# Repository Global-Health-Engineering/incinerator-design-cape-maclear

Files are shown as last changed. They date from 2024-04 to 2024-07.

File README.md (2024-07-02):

# incinerator-design-cape-maclear
<!-- badges: start -->


<!-- badges: end -->

<h1> Development of a Low-Cost Incinerator in Cape Maclear, Malawi </h1>

<b>Contributors</b>  
- Mosè Peduzzi <a href="https://orcid.org/0009-0004-6055-3835">
ORCID logo 0009-0004-6055-3835
</a> *author*  
- Jakub Tkaczuk <a href="https://orcid.org/0000-0001-7997-9423">
ORCID logo 0000-0001-7997-9423
</a> *supervisor, maintainer, developer*  
- Elizabeth Tilley <a href="https://orcid.org/0000-0002-2095-9724">
ORCID logo 0000-0002-2095-9724
</a> *supervisor*  

<p align="middle"> 

<br><br>
<b>Complete description of system design, functionalities, operation, and maintenance is available on:<br \>
<a href="https://global-health-engineering.github.io/incinerator-design-cape-maclear/">Github pages</a>.
</b>
<br><br>
It compliments the openly-accessible master’s thesis, available on the<br \>  
<a href="https://www.research-collection.ethz.ch/handle/20.500.11850/670633">ETH Research Collection</a>
<br><br>
and the introduction video available on<br \>
<a href="https://www.youtube.com/watch?v=6FmEJcynxZE">Youtube</a>.
</p>

# Background

This repository presents the construction of a modified De Montfort Incinerator Mark 8A, designed and built between October and December 2023 in Cape Maclear, Malawi. The incinerator has several modifications implemented, compared to the original design, e.g., the ash collection drawer and the cyclone separator to filter the flue gases.

The construction of the incinerator is part of a broader project conducted by Global Health Engineering, an ETH research group, aiming to introduce regular waste collection in the township of Cape Maclear, Malawi, ensuring safe waste disposal and minimizing environmental contamination. The incinerator constructed within this work reduces waste volume and makes hazardous waste harmless, emphasizing cost-effectiveness.

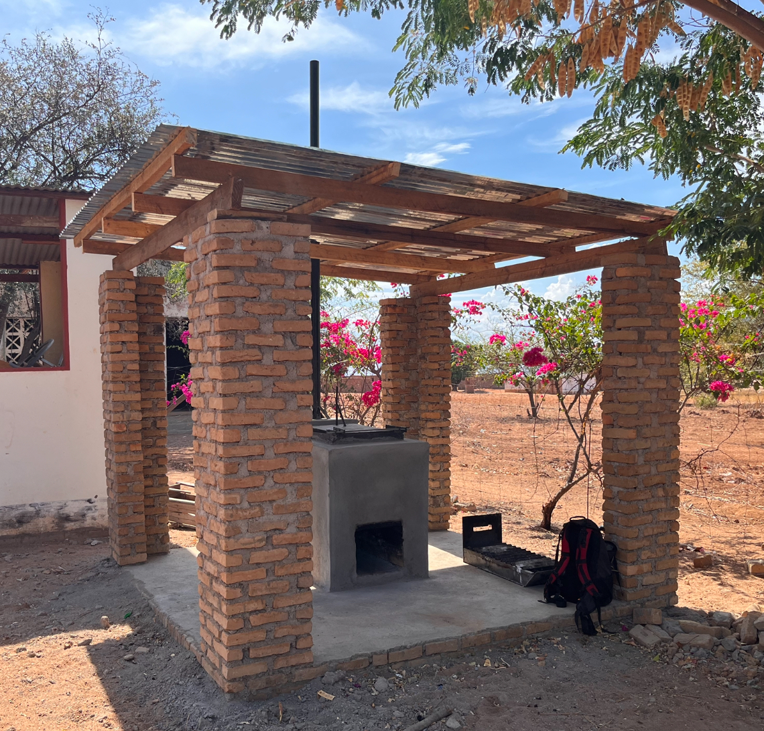
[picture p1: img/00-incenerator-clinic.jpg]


# License

This work is licensed under
[Creative Commons Attribution 4.0 International](https://github.com/Global-Health-Engineering/incinerator-design-cape-maclear/blob/main/LICENSE.md).

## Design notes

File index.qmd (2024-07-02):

---
title: "Low-Cost Incinerator for Cape Maclear, Malawi"
subtitle: "Design, Maintenance, and Operation"
number-sections: true
format: html
---

<!-- badges: start -->


<!-- badges: end -->

<b>Contributors:</b>  
- Mosè Peduzzi <a href="https://orcid.org/0009-0004-6055-3835">
ORCID logo 0009-0004-6055-3835
</a> *author*  
- Jakub Tkaczuk <a href="https://orcid.org/0000-0001-7997-9423">
ORCID logo 0000-0001-7997-9423
</a> *supervisor, maintainer, developer*  
- Elizabeth Tilley <a href="https://orcid.org/0000-0002-2095-9724">
ORCID logo 0000-0002-2095-9724
</a> *supervisor*  

<p align="middle">

<br>
Github repository for this page sits [here](https://github.com/Global-Health-Engineering/incinerator-design-cape-maclear).
</p>

# Introduction {#sec-intro}

This video presents the construction of a modified De Montfort Incinerator Mark 8A, designed and built between October and December 2023 in Cape Maclear, Malawi. The incinerator presents several modifications compared to the original design [^1], e.g., the ash collection drawer [^2] and the cyclone separator to filter the flue gases.

The construction of the incinerator is part of a broader project conducted by Global Health Engineering, an ETH research group, which aims to introduce regular waste collection in the township of Cape Maclear, Malawi, ensuring safe waste disposal and minimizing environmental contamination. This incinerator reduces waste volume and  makes hazardous waste harmless, emphasizing cost-effectiveness.

[^1]: [https://mw-incinerator.info/](https://mw-incinerator.info/)
[^2]: J. Van Den Noortgate, D. Taylor, and G. Yannick, *Incinerator in Health Structures of Low-Income Countries*. Médecins Sans Frontières, 2012. [Link](https://events.development.asia/system/files/materials/2020/04/202004-incineration-health-structures-low-income-countries.pdf).

# Incinerator Overview {#sec-overview}

The incinerator built within this work is a small-size incinerator, composed of a structure of refractory bricks and cement with a metal frame on the top. The interior space is divided into two combustion chambers; the first can be accessed by the operator through a door located at its top, allowing for inserting of a new waste bag. The second combustion chamber and the attached cyclone separator remain inaccessible to the operator and are intended solely for to treat the fumes. The purpose of the second combustion chamber is to reduce carbon monoxide to carbon dioxide through secondary combustion (and combustion time increase), while the cyclone separator allow to reduce the particulate matter (PM) in the fume gasses.

The incinerators can burn about 3.5 kg/h of waste, reaching temperature of 770°C. The mass of the ashes produced by the incinerators represent about 20-30% of total mass of waste burnt.

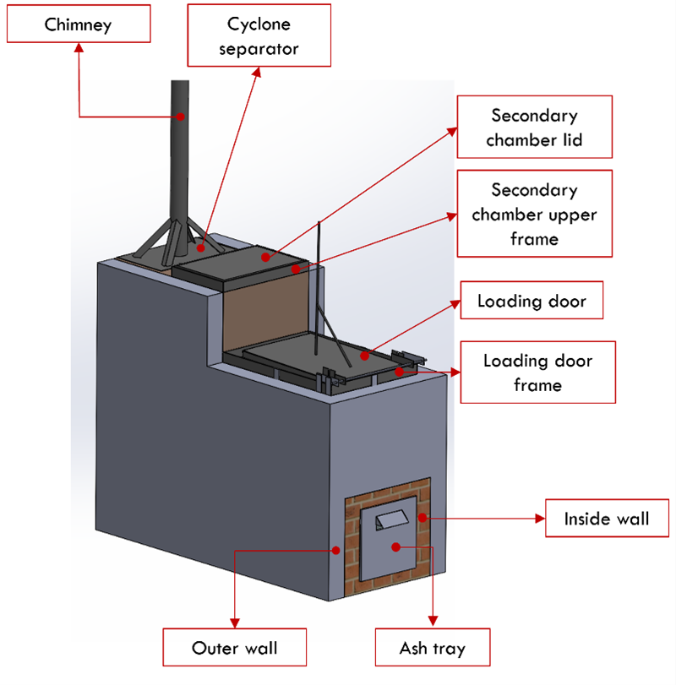
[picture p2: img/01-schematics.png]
Figure 1: Modified De Montfort incinerator Mark 8A with integrated cyclone separator in the back and removable ash tray on the bottom of the combustion chamber.


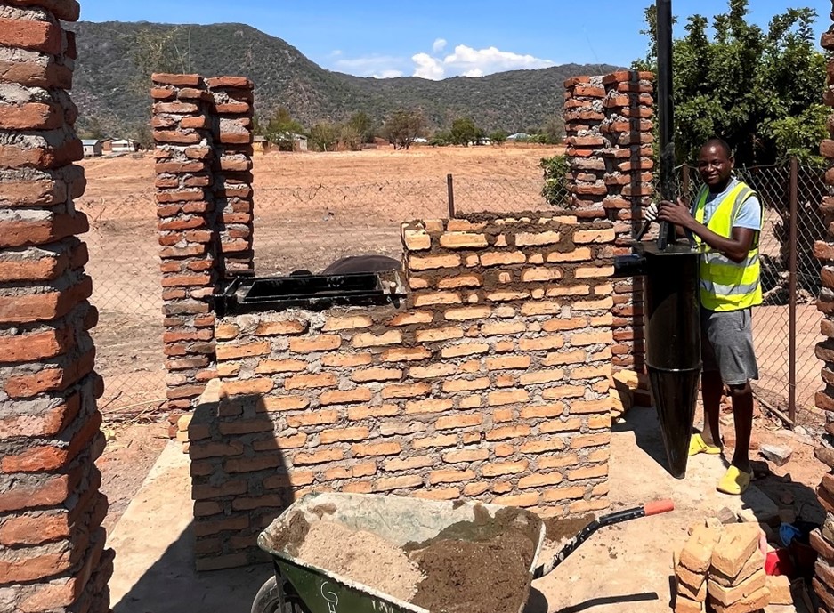
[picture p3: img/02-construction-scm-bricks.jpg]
Figure 2: Incinerator during construction.


# Part List {#sec-part-list}

| No. | Item | Specs | Qty. | Source | Cost per unit (USD) | Total Cost (USD) |
|-----|---|---|---|---|---|---|
| 1 | Metal U-Channel | L x W x H: 100 mm x 60 mm x 6 m | 1 | DeeKay | 85.29 | 85.29 |
| 2 | Angle Iron 30x30x3 mm 6 m | L x W x T: 30 mm x 30 mm x 3 mm x 6 m | 1 | DeeKay | 14.71 | 14.71 |
| 3 | Metal plate | L x W x H: 2400 mm x 1200 mm x 3 mm | 1 | DeeKay | 126.47 | 126.47 |
| 4 | Metal tube with a diameter| D x L: 75 mm x 3 m | 1 | DeeKay | 46.76 | 46.76 |
| 5 | Flat bar | L x W x H: 35 mm x 3 mm x 6 m | 1 | DeeKay | 17.35 | 17.35 |
| 6 | Heat resistent paint | 1 L | 1 | Valmore Paints | 7.47 | 7.47 |
| 7 | Threaded Rod | D x L: M 10 x 1 m | 1 | Build Africa | 6.62 | 6.62 |
| 8 | Bolt | M 10 | 10 | Lilongwe | 0.12 | 1.18 |
| 9 | Washer | M 10 | 2 | Lilongwe | 0.12 | 0.24 |
| 10  | Empty oil barrel | 200 L | 1 | Ndirande market  | 17.65 | 17.65 |
| 11  | Cement bag | 50 kg | 8 | Monkey bay | 11.76 | 94.12 |
| 12  | Sand | 1 ton | 2 | Cape Maclear | 2.94 | 5.88 |
| 13  | Bricks (njeli) | L x W x H: 10 cm x 17 cm x 6 cm | 1200 | Cape Maclear | 0.03 | 31.76 |
| 14  | Armament bar | D x L: 10 mm x 12 m | 1 | DeeKay | 11.76 | 11.76 |
| | **Total Costs (USD)** | | | | | **467.26** |

# Safety Precautions {#sec-safety}

Always wear protective equipment when working with the incinerator. Goggles, gloves, and closed footwear are essential for protecting the operator’s health.

# License {#sec-license}

The complete design and user manual are licensed under [Creative Commons Attribution 4.0 International](https://github.com/Global-Health-Engineering/incinerator-design-cape-maclear/blob/main/LICENSE.md).

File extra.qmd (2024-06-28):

---
title: "Extra"
number-sections: true
format: html
---

# Ash pit {#sec-ash-pit}

To minimize contamination of the environment, an ash pit has to be built. Search for older structures made of cement, such as old pit latrines or septic tanks. If you do not find any, build a pit, using bricks and cement to safely disposed of the ashes (in enclosed space, preventing leakage to soil). Empty oil drums can be used instead - once filled wit ashes, close and bury them.

In this project an old pit latrine was used with a lid additionally. Using the leftover of the roof, a structure made of wood was assembled, on which two metal meshes were laid, finer mesh at the bottom and more robust one formed from the reinforcement bars above. The construction steps are shown in Figures 1, 2, and 3.

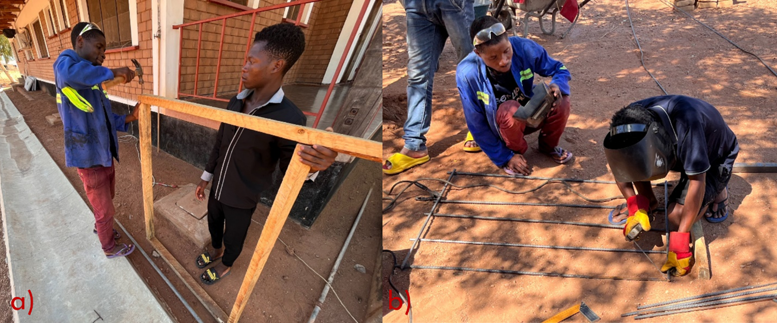
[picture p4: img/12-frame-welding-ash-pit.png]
Figure 1: Two workers building the stamp for the ash pit cover (a); welder building the reinforcement mesh for the ash pit cover.


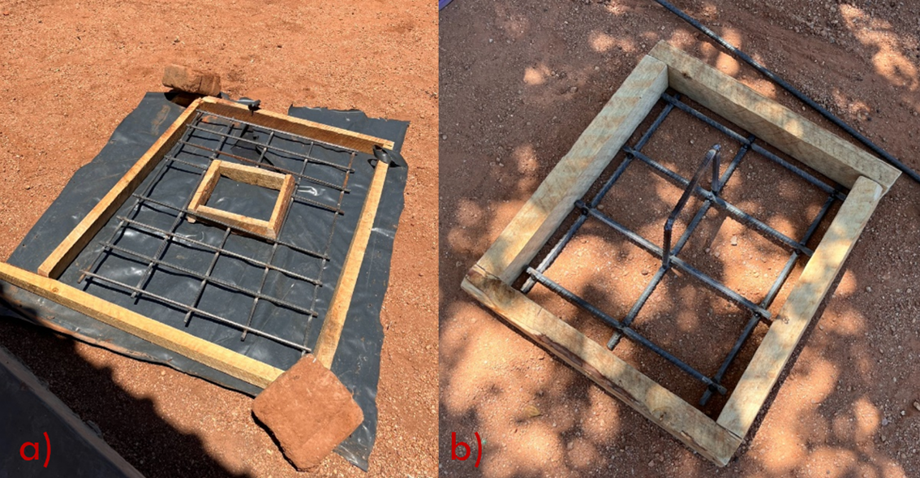
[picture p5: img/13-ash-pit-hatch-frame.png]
Figure 2: Ash pit cover stamp and mesh (a); ash pit cover loading door stamp and reinforcement mesh (b).


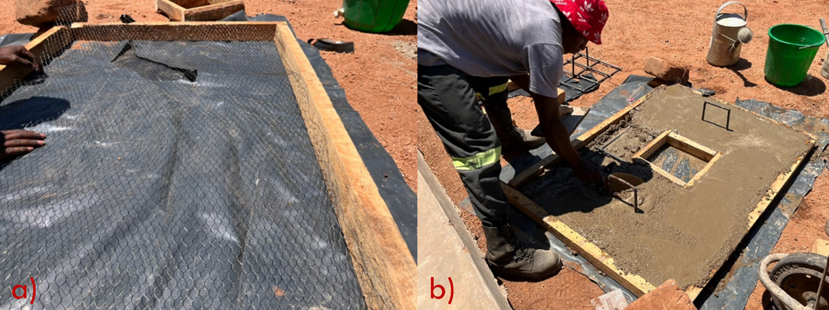
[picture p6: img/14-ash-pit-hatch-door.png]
Figure 3: Fine mesh as bottom of the ash pit cover (a); Bricklayer filling the stamp of the ash pit cover (b).


Both the cover, and the loading door are filled with cement and wetted every 4 hours for one day. Waiting time of one more day ensures complete bonding of concrete, after which the cover and the loading door can be installed above the pit (see Figure 4).

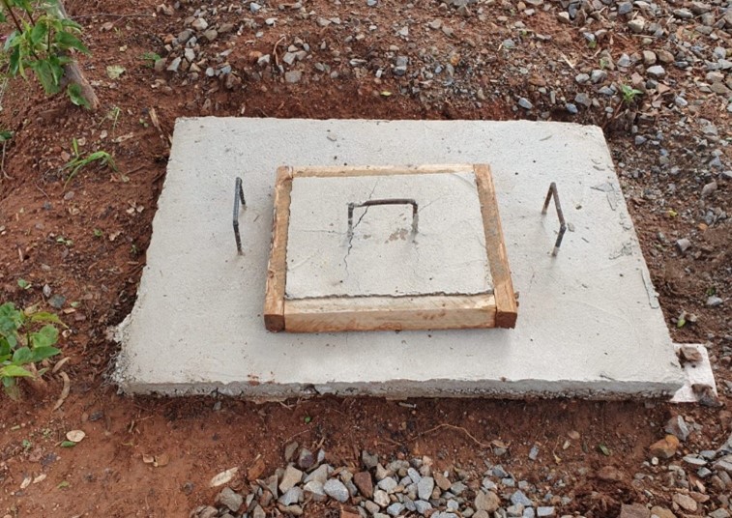
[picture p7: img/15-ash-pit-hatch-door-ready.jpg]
Figure 4: Ash pit cover with loading door set in place over the old latrine.


# Roof {#sec-roof}

The construction of the roof protects the incinerator from weather conditions, ensuring its greater longevity. Its costs is around 157 USD and takes between 2 and 4 days.

Four robust pillars should be build with bricks and cement, do not skimp on bricks and concrete. Choose the side on which you want the water to be drained and make sure that the columns on that side are around 10 cm shorter than on the opposite side. Insert a metal wire, when constructing the top section of each column, to later anchor the timber. Once the column are completed, let them dry for at least one day, before starting the work on roofing.

The wooden beams (2" $\times$ 4") should connect two pairs of columns at their tops. Aanchor the beams to the columns with the earlier integrated wire. Lay four perpendicular beams of the same size on top of the two timber beams equally dividing the roof area. Add one more layer of four, equally spaced, perpendicular to the preceding layer, beams. Place the corrugated iron sheet on top of the beams.

A hole needs to be cut to route the chimney though the roof. A flashband can be used to prevent water leaking between the chimney and the roof.

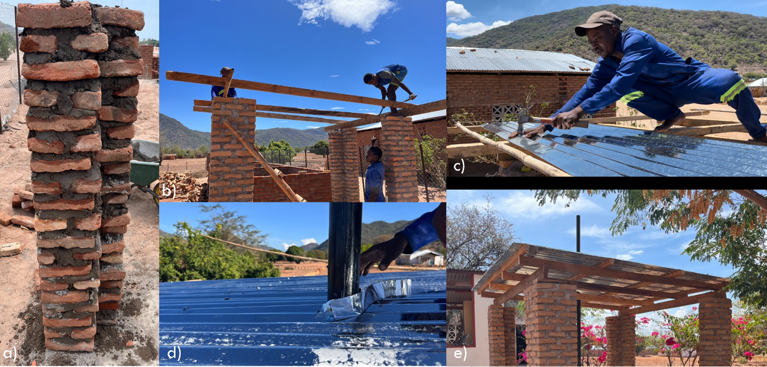
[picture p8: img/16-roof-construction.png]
Figure 5: Roof construction: (a) column; (b) wood structure anchored to the top of columns at 2.2 m height; (c) corrugated iron sheet attached to the wooden beams with nails; (d) flashband sealing the hole for the chimney; (e) complet roof.


## Material list {#sec-roof-materials}

| No. | Item | Specification | Qty. | Source | Cost per unit (USD) | Total Cost (USD) |
|-----|---|---|---|---|---|---|
| 1 | Cement bag | 50 kg | 1 | Monkey bay| 12.22 | 12.22 |
| 2 | Roof nails | 1 kg | 2 | Monkey bay| 2.17 | 4.33 |
| 3 | Corrugated iron sheet | L $\times$ W: 305 cm $\times$ 75 cm | 7 | Monkey bay| 5.78 | 40.44 |
| 4 | Sand | 1 ton | 0.5  | Monkey bay| 2.78 | 1.39 |
| 5 | Bricks | L $\times$ W $\times$ H: 10 cm $\times$ 17 cm $\times$ 6 cm | 700  | Monkey bay| 0.03 | 17.50 |
| 6 | Roof wires | D $\times$ L: 2.5 mm $\times$ 6 m | 1 | Monkey bay| 1.11 | 1.11 |
| 7 | Timber 2" $\times$ 3" | L $\times$ W $\times$ H: 5 cm $\times$ 7.6 cm $\times$ 4 m  | 4 | Monkey bay| 5.56 | 22.22 |
| 8 | Timber 2" $\times$ 4" | L $\times$ W $\times$ H: 5 cm $\times$ 10 cm $\times$ 4 m | 4 | Monkey bay| 6.94 | 27.78 |
| 9 | Timber 2" $\times$ 6" | L $\times$ W $\times$ H: 5 cm $\times$ 15 cm $\times$ 4 m | 2 | Monkey bay| 8.33 | 16.67 |
| 10  | Flashband/Rubberwise 30 cm  | 2 m | 1 | Monkey bay| 1.94 | 1.94 |
| | **Total Costs (USD)** | | | | | **145.61** |

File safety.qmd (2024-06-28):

---
title: "Safety Precautions"
number-sections: true
format: html
---

# Safety during construction {#sec-safety-construction}

Wear safety glasses and working gloves when using the angle grinder or other power tools.

Make sure to use safety equipment during welding: passive UV protection glasses of class EN 169 or automatic glasses of class EN 379 to protect your eyes. Wear heat resistant gloves and colthing covering your full body, forearms and legs in particular. If you use an electrode/stick welding machine, make sure to work in a ventilated place. 

# Safety during operation {#sec-safety-operation}

Wear the following:  
- long clothes, fire retardant and acid resistant, if possible;  
- safety goggles;  
- heat resistant gloves;  
- rubber boots;  
- filtering mask, with carbon active filters, if possible.

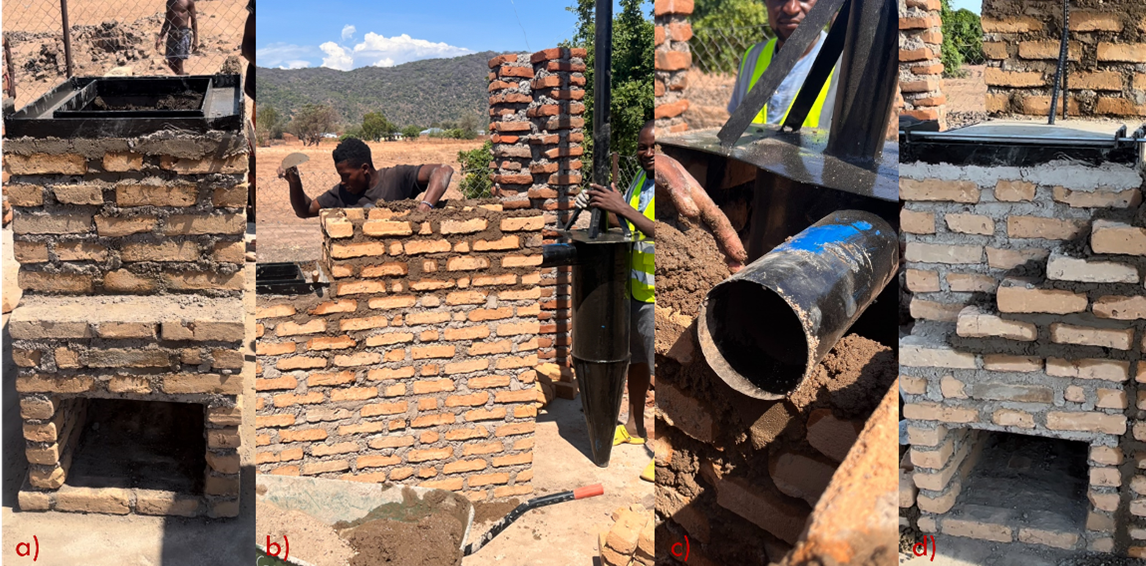
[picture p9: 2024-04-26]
img/11-semi-finished-4-figs.png

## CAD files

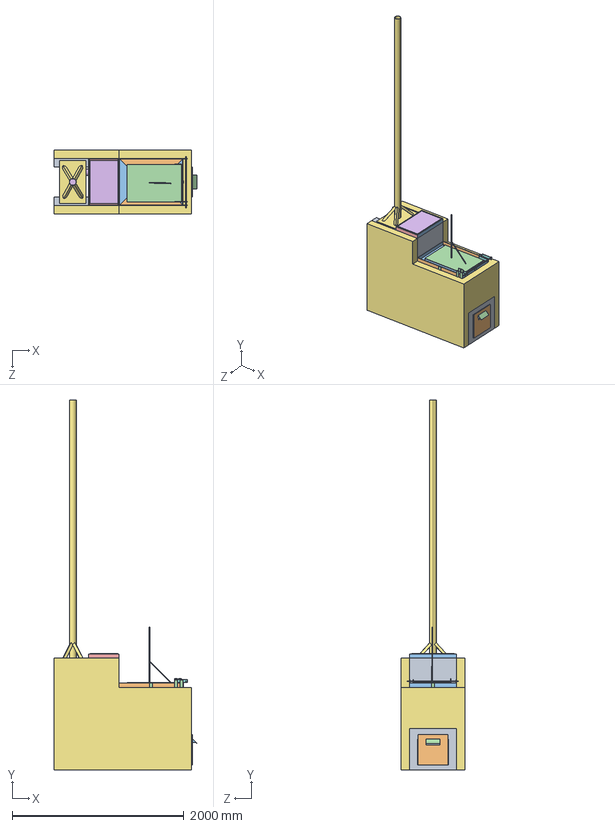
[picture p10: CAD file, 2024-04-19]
cad/de_montfort_incinerator_with_cyclone_separator.step
1659.5 x 4303.0 x 745.0 mm
Sustainable_body
due x 2
uno x 4
Connection_plate x 11
tre x 2
CycloneSeparator
Chimney
door connection x 4
Threaded_bar
Loading door plate
Door_handle_long
SecondaryChamberCover
AshTRay_O
AshTray_N x 2
AshTray_P
AshTray_I
AshTray_M x 2
AshTray_L
AshTray_grid
OuterWallSustainable

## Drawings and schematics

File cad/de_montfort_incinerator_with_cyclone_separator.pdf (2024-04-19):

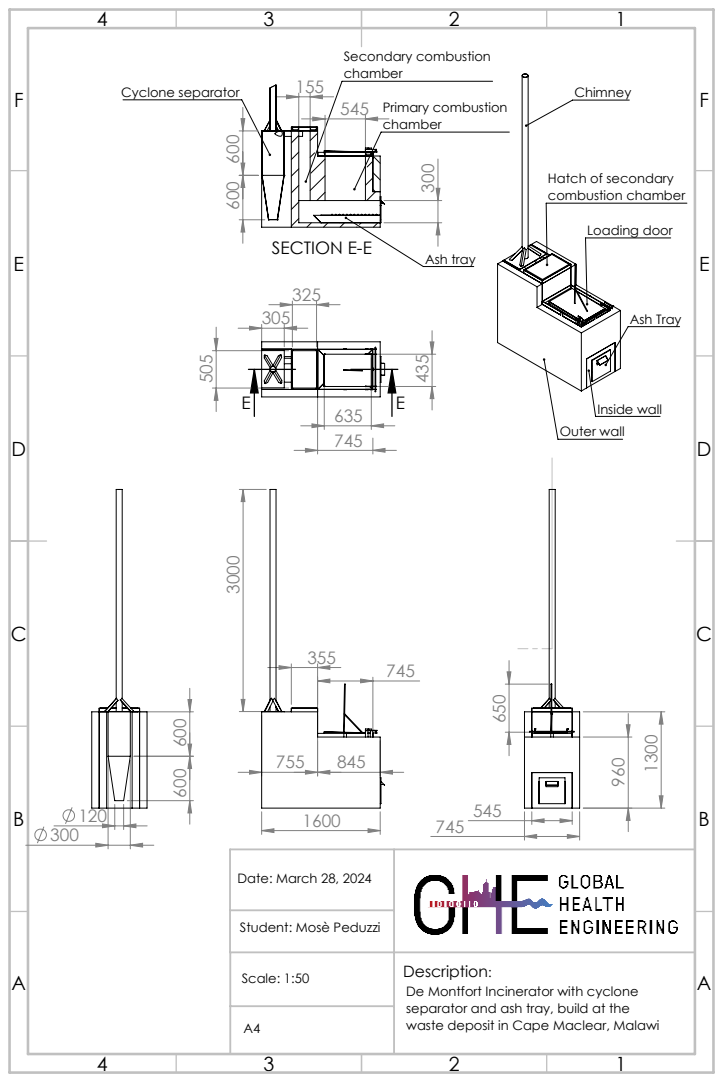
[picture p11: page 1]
Ash Tray; Loading door; Outer wall; Inside wall; SECTION E-E; Primary combustion; Secondary combustion; Cyclone separator; Ash tray; Date: March 28, 2024; Scale: 1:50

Hatch of secondary
combustion chamber

Student: Mosè Peduzzi

Description:
De Montfort Incinerator with cyclone
separator and ash tray, build at the
waste deposit in Cape Maclear, Malawi

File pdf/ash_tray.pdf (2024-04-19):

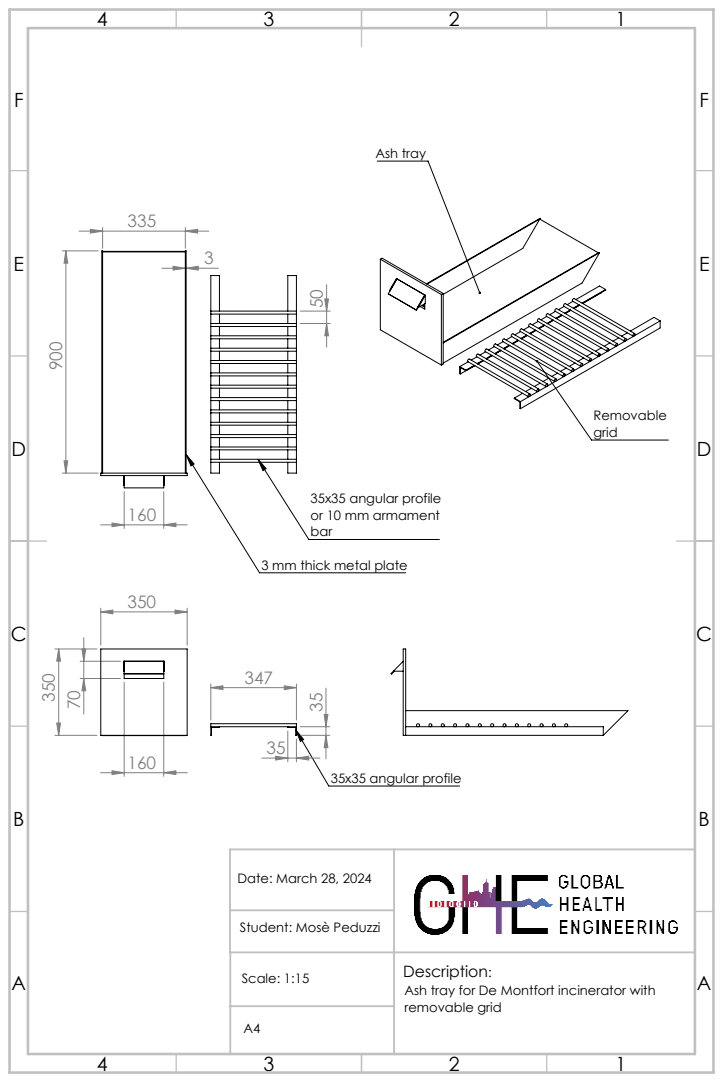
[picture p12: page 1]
35x35 angular profile; Ash tray; Scale: 1:15

35x35 angular profile
or 10 mm armament
bar
3 mm thick metal plate

Date: March 28, 2024

Student: Mosè Peduzzi

Description:
Ash tray for De Montfort incinerator with
removable grid

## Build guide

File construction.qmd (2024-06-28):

---
title: "Construction"
number-sections: true
format: html
---

Complete dimensions of the incinerator with cyclone separator are available in the in Figure 1. CAD model of the assembly and the pdf version of this drawing are available in the Github repository in the [`cad`](https://github.com/Global-Health-Engineering/incinerator-design-cape-maclear/tree/main/cad) directory.

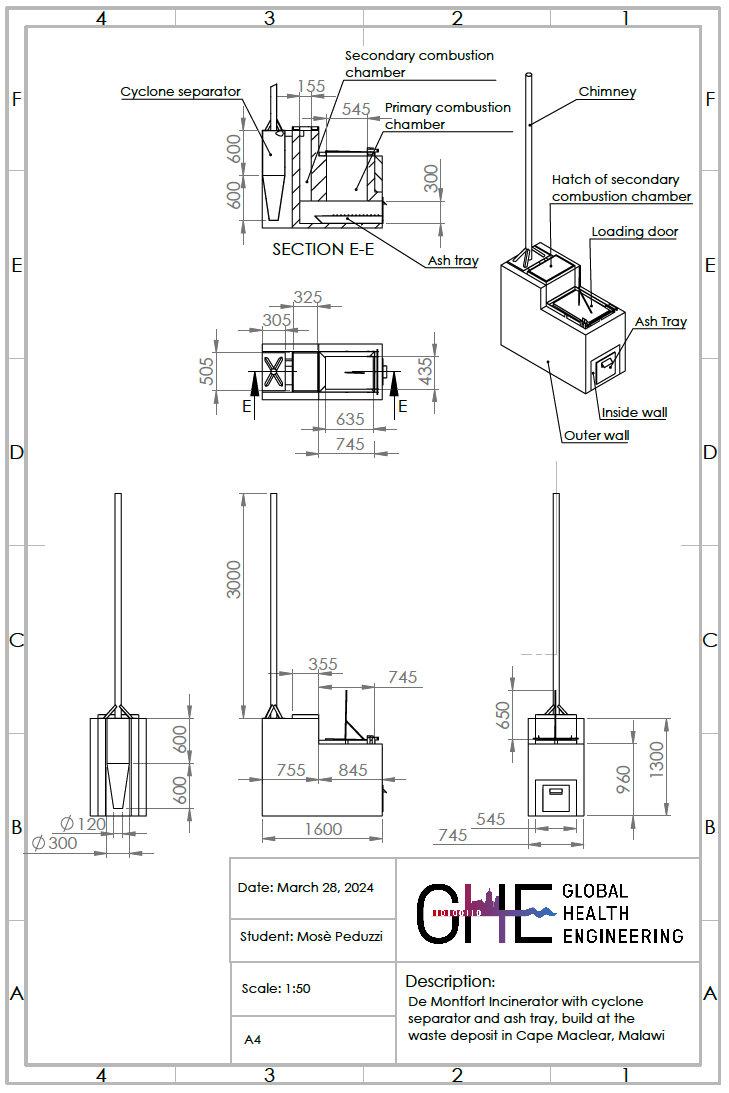
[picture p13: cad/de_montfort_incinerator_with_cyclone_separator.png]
Figure 1: CAD drawing of the complete incinerator's assembly.


The first step in the construction of the incinerator is the fabrication of the metal parts, these include:

**ash tray**, composed of a box made of 3 mm-thick metal plates, welded together with a removable grid, build from two angular profiles on the sides. They are connected with a 10 mm armament bar creating a grid on which the unburned waste lays (see Figure 2 for exact dimensions and Figure 3 for construction details).

**loading door and its frame**, which allow for an easy access to the primary combustion chamber. The loading door is composed of a 3 mm steel plate with angular profiles on the sides. The door is connected to the frame with a hinge and a M 10 threaded bar. The frame has a U-shaped cross-section to seal the movable parts with sand placed in the U-shaped channel.

**cover of the secondary combustion chamber and its frame**, which allow to close the secondary combustion chamber with a steel plate that is free to dilatate without avoiding leaking of gas and breaking the incinerator's concrete walls.

**cyclone separator**, which was built from a 200 l empty oil drum, cut by hand with shears, a hammer, and a chisel. The barrel has to be opened to create three pieces: the central, cylindrical body, the lower cone, and the inlet tube. The parts needs to be welded together and attached to the chimney and the support plate (see Figure 4 for construction deatils).

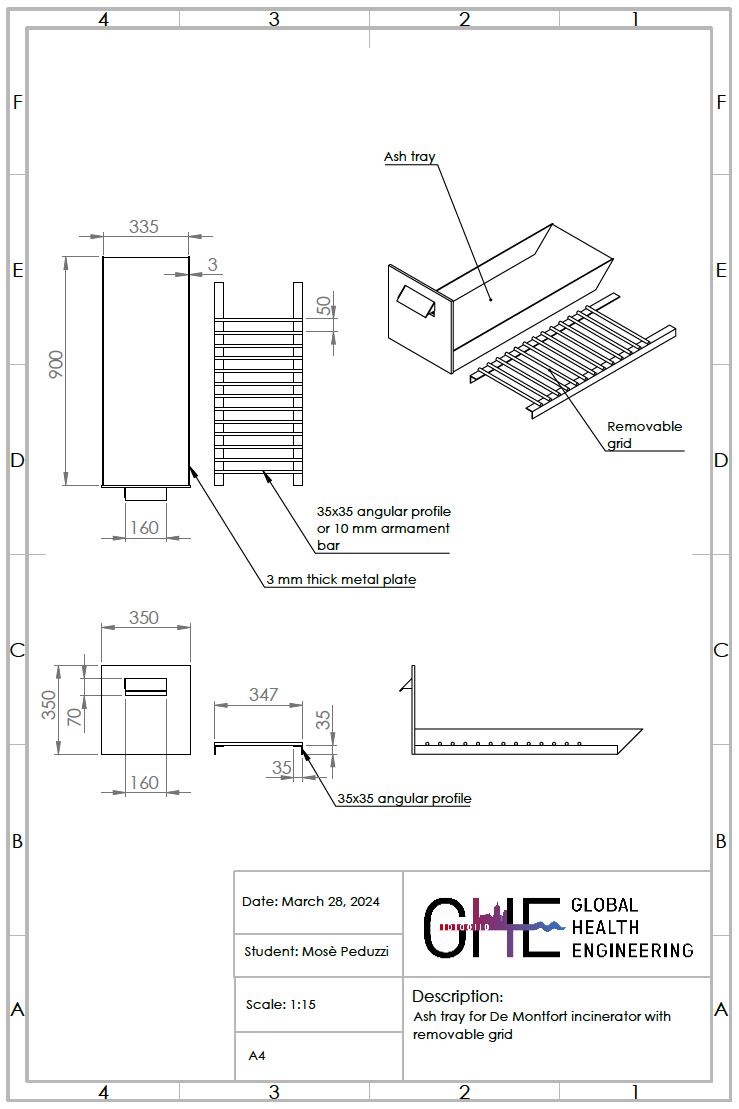
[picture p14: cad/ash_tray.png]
Figure 2: CAD drawing of the ash tray.


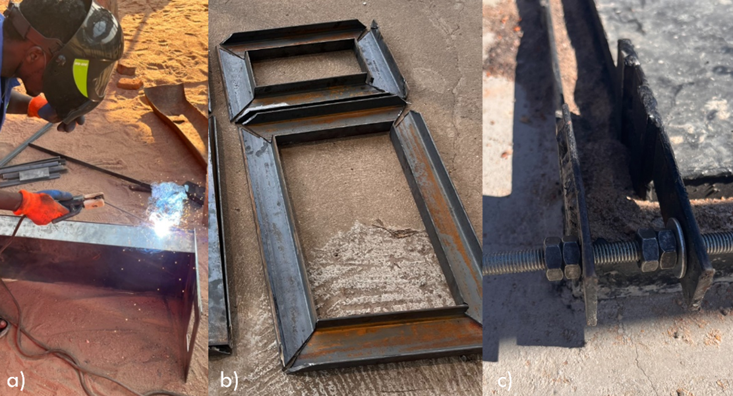
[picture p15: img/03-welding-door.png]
Figure 3: Ash tray in production. a) Welding. b) Loading door frame cut and ready for welding. c) Hinge between the and the frame.


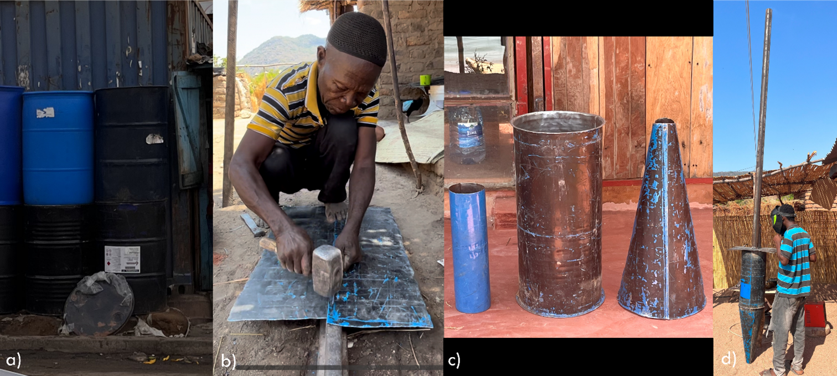
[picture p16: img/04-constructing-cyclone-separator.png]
Figure 4: Four step of the production of the cyclone separator: a) Empty oil drums at the market in Blantyre. b) Drum cutting and piece assembly. c) Pieces produced from the drum. d) Welding of all parts and painting.


All the steel parts have to be painted with a heat resistant paint to prevent them from rusting.

Once all the metal parts are completed, the work at the construction site starts. To elevate the incinerator from the ground and give the all structure more stability, a base of 3 m $\times$ 3 m has to be built. 8 nails and a string are used to set the boundaries of the base, as shown in Figure 5. Figure 6 shows the place for the incinerator's construction.

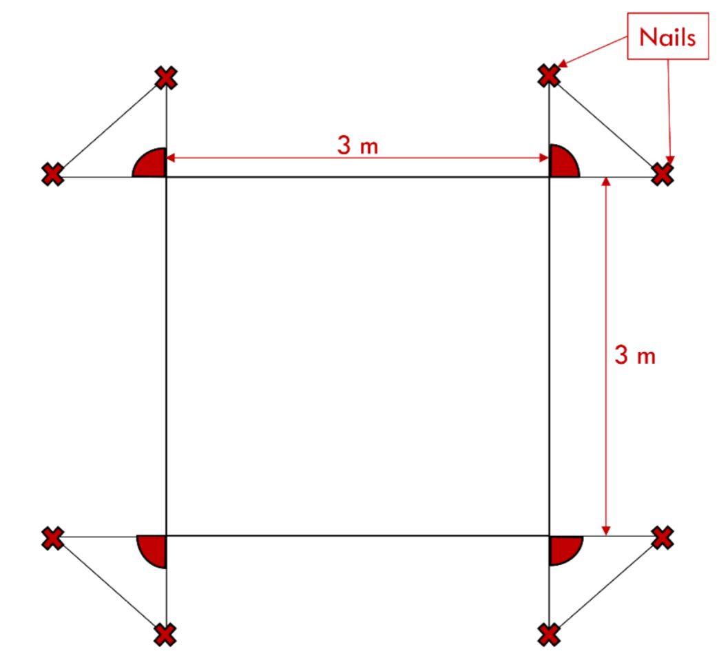
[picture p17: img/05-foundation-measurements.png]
Figure 5: Scheme visualizing the nail placement and the string to start setting up the foundation of the base.


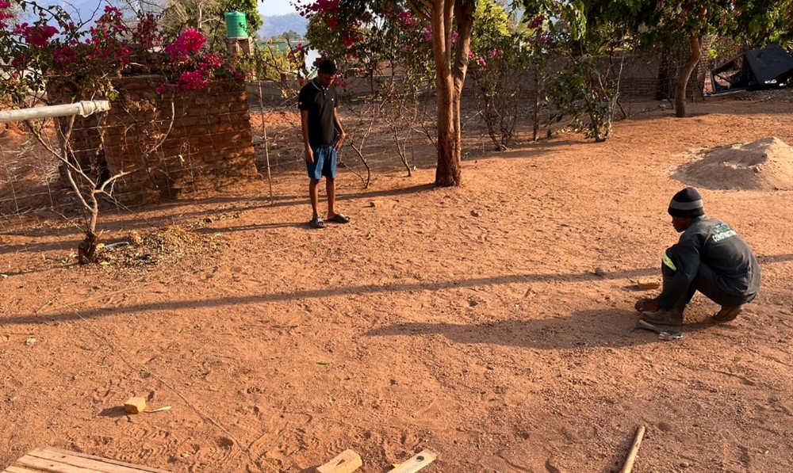
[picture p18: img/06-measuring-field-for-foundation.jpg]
Figure 6: Bricklayers set in place nails and string before starting the construction at the Billy Riordan Memorial Clinic.


Once the string is in place, the outer structure shall be built with bricks and cement, starting from the corners. Steps in foundation construction are shown in Figure 7.

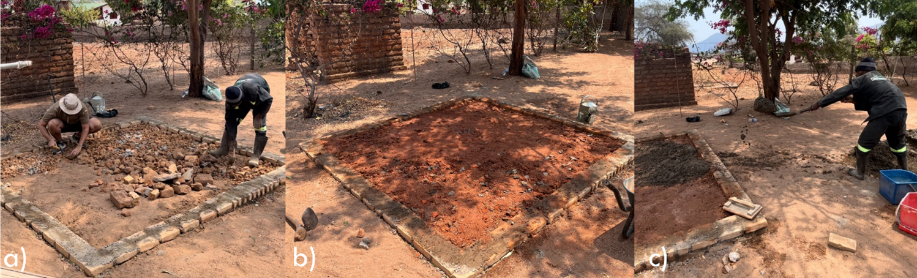
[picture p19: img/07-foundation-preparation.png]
Figure 7: First steps in building the foundation: a) Filling the inner space of the foundation with broken bricks and stones the size of a fist. b) Cover everything with a layer dirt and wet it. c) Cover everything with a layer of cement.


The inner part of the structure is filled with stones and broken bricks in the size of a fist, then covered with dirt and watered. In the end, everythin is covered with a layer of cement - a sponge and a trowel are used to smooth out the surface. Because of expected high temperatures coming from the incineration chamber, and exposure to the sun, it is important to slow the drying of cement by wetting it continuousely for 24 hours. At least 48 hours must pass, after completion of the base, before the first bricks can be laid.

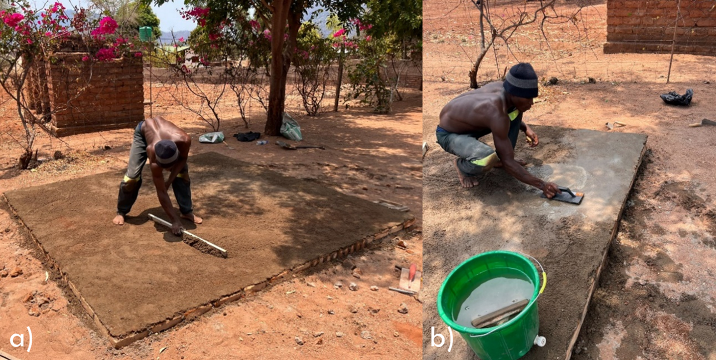
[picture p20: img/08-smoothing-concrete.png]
Figure 8: Last finishing touches of the base: a) wet cement being smoothed. b) drying cement being smoothed with a sponge and a trowel.


To elevate the drawer from the floor and facilitate its motion, a small base made of bricks and cement, is build following this schematic layout from Figure 9.

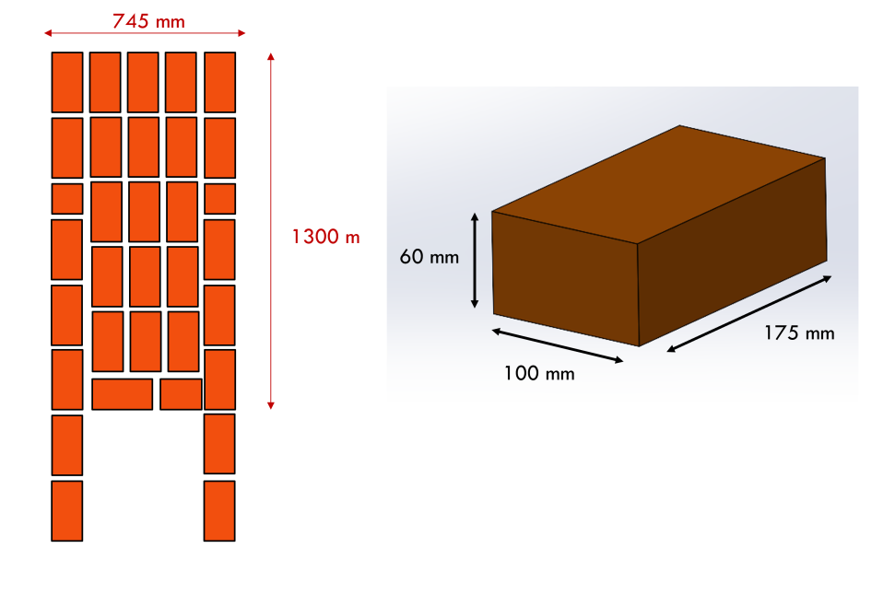
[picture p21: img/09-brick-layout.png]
Figure 9: Scheme showing the layout of the bricks, and their size, for the base of the incinerator.


On this small base, the ash drawer is placed and used as a reference to lay the first layer of bricks of the combustion chamber wall.

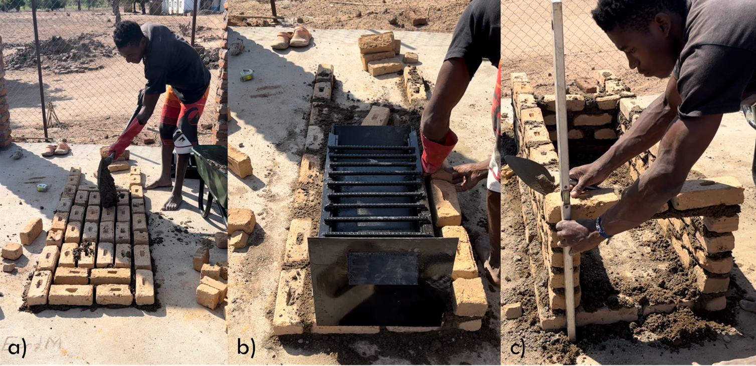
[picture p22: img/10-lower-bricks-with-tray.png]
Figure 10: Construction beginning: a) Bricks laid over a thin layer of cement. b) Ash tray set in place on the first layer of bricks, used as reference to build the inner wall of the incinerator. c) Wall reaches 30 cm in height, where the steel bars are used are crossbars.


The wall is raised untill it is 30 cm high. At this height reinforcement bars are inserted over the wall using cement, and serving as crossbars. With the created crossbars, the walls are raised untill they reach 1 m in height, when the frame for the loading door can be installed in place with cement.

The walls of the secondary chamber are raised to the height of 1.3 m. Later, the cyclone separator and upper frame of the secondary chamber can be incorporated into the structure. 

Once all the parts are set in place and dry, a second layer of bricks is put in place. It is attached to the first one to confer more robustness to the whole structure (see Figure 11).

![Figure 11: Consecutive construction phases: a) Frame of the loading door embedded within the structure at an height of 1 m. b) Secondary combustion chamber walls raised to the height of 1.3 m and the cyclone being put in place. c) Inlet tube to the cyclone separator being integrated into the back wall of the secondary combustion chamber. d) The outside wall under construction, covering the inner wall.](img/10-lower-bricks-with-tray.png)

Plastering work and a roof remain optional and of little impact to the operational conditions of the incinerator itself (more information on them is available in section <a href="https://global-health-engineering.github.io/incinerator-design-cape-maclear/operation-maintenance.html">Extra</a>).

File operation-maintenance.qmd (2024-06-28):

---
title: "Prototype Operation & Maintenance"
number-sections: true
format: html
---

# Operation {#sec-operation}

This section briefly explains the steps to be followed for proper use of the incinerator. To operate it:

1. Wear working clothes with long sleeves (better if fire retardant and acid resistant), closed shoes (preferably rubber boots), safety goggles, and a face mask. 
2. Once sure that the incinerator is cold, pull out the ash drawer, remove the grate and empty the contents into the ash containment pit. Use a shovel or a broom to remove any trash/ashes stuck to the bottom of the tray. Check the interior of the incinerator and remove any waste from inside the incinerator chamber.
3. Place back the empty ash tray with the grate inside the primary combustion chamber.
4. Open the loading door and fill half of the combustion chamber with waste. Make sure there are no light bulbs, batteries or paint cans as they may explode during combustion, damaging the structure and causing serious injury.
5. Light a piece of paper or cardboard and insert it inside the primary combustion chamber.
6. Close the loading door.
7. A waste bag of about 40 liters can be inserted every 30 minutes.
8. Once the usage cycle is done, make sure that the loading door is closed and the ash tray is inside the primary combustion chamber until the incinerator cools down complitely.

# Maintenance {#sec-maintenance}

To ensure longevity of the incinerator, maintenance, as specified below, is essential.

1. Weekly Inspection - check the state of the primary nd secondary combustion chambers, the inlet tube to the cyclone separator, and the cyclone. Make sure to change the sand used to seal the loading door once and the lid of the secondary combustion chamber, once it is burned.
2. Monthly Inspection - search for rusting points and paint them with heat resistant paint. Check for moving bricks and fix them in place with cement.
3. Year Inspection - Substitute broken or heavily rusted parts.

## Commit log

2024-04-19 add drawings and step
    [De_Montfort_Incinerator_Cyclone_Separator.STEP]
2024-06-28 update qmd readme
    [de_montfort_incinerator_with_cyclone_separator.step]

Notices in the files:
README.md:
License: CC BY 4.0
